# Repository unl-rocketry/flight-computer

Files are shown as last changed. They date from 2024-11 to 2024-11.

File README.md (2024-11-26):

# Flight Computer
A versatile, inexpensive, modular, and **open source** flight computer and altimeter
system for amateur and experimental rocketry.

All designs in this repository are licensed under the [**CERN-OHL-S v2 or any later 
version**](https://ohwr.org/project/cernohl/-/wikis/uploads/b236492596cfc91c12def7d50bbf7da0/cern_ohl_s_v2.pdf). 
Contributions are welcome!

# Core Board
This design should be capable of using input voltages from 3v → 16v on the
battery input to allow for a wide range of batteries to be used. It is designed
to control and independently fire up to 3 individual high power in-flight events
(eg. ejection charges).

## Built-in Sensors
The sensor package includes a Bosch BNO055 motion co-processor for acceleration,
magnetic heading, and 3d orientation. It also includes a Bosch BME280 sensor for
pressure (along with altitude), temperature, and humidity measurements. These
sensor measurements can be used for flight control, and can also be logged to a
MicroSD card mounted on the board for ease of data recovery.

## Toolchain Support
All programmable components of this board were selected to be compatible with
Rust-based microcontroller frameworks like Embassy, for ease of programming and
future extension of software capabilities.

## Images
front

back

# Expansion Modules
A major feature of the Core Board is the ability to be expanded by
connecting via an I2C (and hopefully in the future CAN Bus) connection to other
boards and sensors with the same connectors. These expansion  boards could
provide additional capabilities while being modular for quickly swapping and
replacing parts.

The connectors on the Core Board are compatible with any Adafruit Stemma QT or 
SparkFun Qwiic board, which immediately provides for a lot of options for
sensors without any design or soldering work needed.

In the future, this repository will host the KiCad files for expansion boards
created by UNL Aerospace Rocketry.

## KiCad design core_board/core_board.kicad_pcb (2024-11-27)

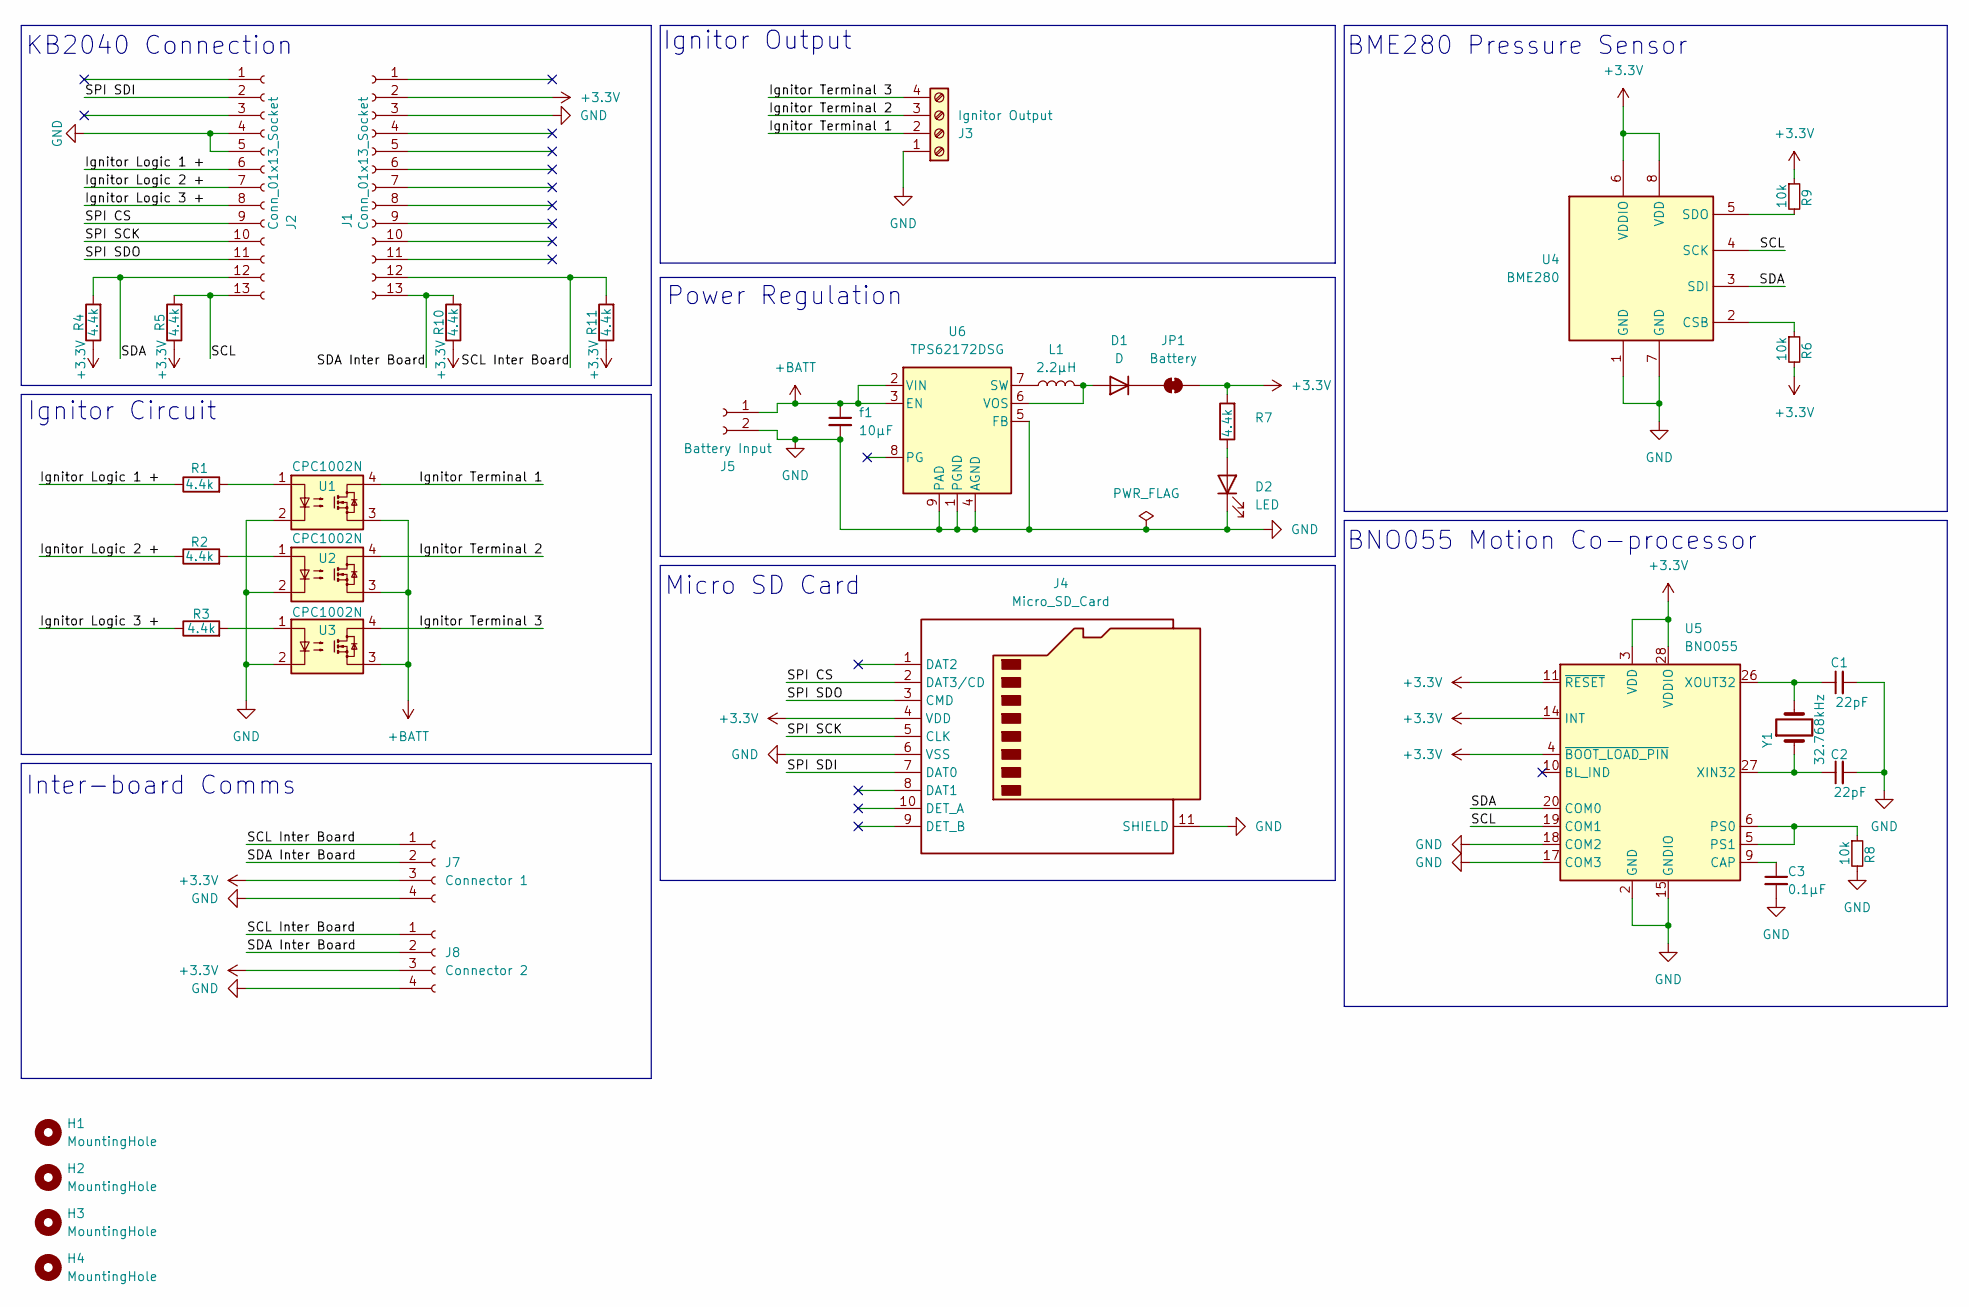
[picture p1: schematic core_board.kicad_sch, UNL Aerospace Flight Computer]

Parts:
C1, C2: 22pF; C_0603_1608Metric_Pad1.08x0.95mm_HandSolder
C3: 0.1µF; C_0603_1608Metric_Pad1.08x0.95mm_HandSolder
D1: D; D_0603_1608Metric_Pad1.05x0.95mm_HandSolder
D2: LED; LED_0603_1608Metric_Pad1.05x0.95mm_HandSolder
H1, H2, H3, H4: MountingHole; MountingHole_2.2mm_M2_ISO7380_Pad
J1, J2: Conn_01x13_Socket; PinHeader_1x13_P2.54mm_Vertical
J3: Ignitor Output; TerminalBlock_Phoenix_MPT-0,5-4-2.54_1x04_P2.54mm_Horizontal
J4: Micro_SD_Card; microSD_HC_Hirose_DM3D-SF
J5: Battery Input; JST_PH_S2B-PH-K_1x02_P2.00mm_Horizontal
J7: Connector 1; JST_SH_BM04B-SRSS-TB_1x04-1MP_P1.00mm_Vertical-CUSTOM
J8: Connector 2; JST_SH_BM04B-SRSS-TB_1x04-1MP_P1.00mm_Vertical-CUSTOM
JP1: Battery; SolderJumper-2_P1.3mm_Bridged_Pad1.0x1.5mm
L1: 2.2µH; L_0603_1608Metric_Pad1.05x0.95mm_HandSolder
R1, R2, R3, R4, R5, R7, R10, R11: 4.4k; R_0603_1608Metric_Pad0.98x0.95mm_HandSolder
R6, R8, R9: 10k; R_0603_1608Metric_Pad0.98x0.95mm_HandSolder
U1, U2, U3: CPC1002N; SOP-4_3.8x4.1mm_P2.54mm
U4: BME280; Bosch_LGA-8_2.5x2.5mm_P0.65mm_ClockwisePinNumbering
U5: BNO055; LGA-28_5.2x3.8mm_P0.5mm
U6: TPS62172DSG; WSON-8-1EP_2x2mm_P0.5mm_EP0.9x1.6mm_ThermalVias
Y1: 32.768kHz; Crystal_SMD_G8-2Pin_3.2x1.5mm_HandSoldering
f1: 10µF; C_0805_2012Metric_Pad1.18x1.45mm_HandSolder

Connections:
+3.3V: J1.2, J4.4 (VDD), J7.3, J8.3, JP1.2 (B), R4.1, R5.1, R6.2, R7.2, R9.1, R10.1, R11.1, U4.6 (VDDIO), U4.8 (VDD), U5.3 (VDD), U5.4 (~BOOT_LOAD_PIN), U5.11 (~RESET), U5.14 (INT), U5.28 (VDDIO)
+BATT: J5.1, U1.3, U2.3, U3.3, U6.2 (VIN), U6.3 (EN), f1.1
/Ignitor Logic 1 +: J2.6, R1.1
/Ignitor Logic 2 +: J2.7, R2.1
/Ignitor Logic 3 +: J2.8, R3.1
/Ignitor Terminal 1: J3.2, U1.4
/Ignitor Terminal 2: J3.3, U2.4
/Ignitor Terminal 3: J3.4, U3.4
/SCL: J2.13, R5.2, U4.4 (SCK), U5.19 (COM1)
/SCL Inter Board: J1.12, J7.1, J8.1, R11.2
/SDA: J2.12, R4.2, U4.3 (SDI), U5.20 (COM0)
/SDA Inter Board: J1.13, J7.2, J8.2, R10.2
/SPI CS: J2.9, J4.2 (DAT3/CD)
/SPI SCK: J2.10, J4.5 (CLK)
/SPI SDI: J2.2, J4.7 (DAT0)
/SPI SDO: J2.11, J4.3 (CMD)
GND: C1.2, C2.2, C3.2, D2.1 (K), J1.3, J2.4, J2.5, J3.1, J4.6 (VSS), J4.11 (SHIELD), J5.2, J7.4, J8.4, R8.2, U1.2, U2.2, U3.2, U4.1 (GND), U4.7 (GND), U5.2 (GND), U5.15 (GNDIO), U5.16 (GNDIO), U5.17 (COM3), U5.18 (COM2), U5.25 (GNDIO), U6.1 (PGND), U6.4 (AGND), U6.5 (FB), U6.9 (PAD), f1.2
unnamed: D1.2 (A), L1.2, U6.6 (VOS)
unnamed: D1.1 (K), JP1.1 (A)
unnamed: D2.2 (A), R7.1
unnamed: R1.2, U1.1
unnamed: R2.2, U2.1
unnamed: R3.2, U3.1
unnamed: R6.1, U4.2 (CSB)
unnamed: R9.2, U4.5 (SDO)
unnamed: C3.1, U5.9 (CAP)
unnamed: R8.1, U5.5 (PS1), U5.6 (PS0)
unnamed: C2.1, U5.27 (XIN32), Y1.1
unnamed: C1.1, U5.26 (XOUT32), Y1.2
unnamed: L1.1, U6.7 (SW)

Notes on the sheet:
Inter-board Comms
Micro SD Card
Ignitor Circuit
Power Regulation
KB2040 Connection
BME280 Pressure Sensor
Ignitor Output
BNO055 Motion Co-processor

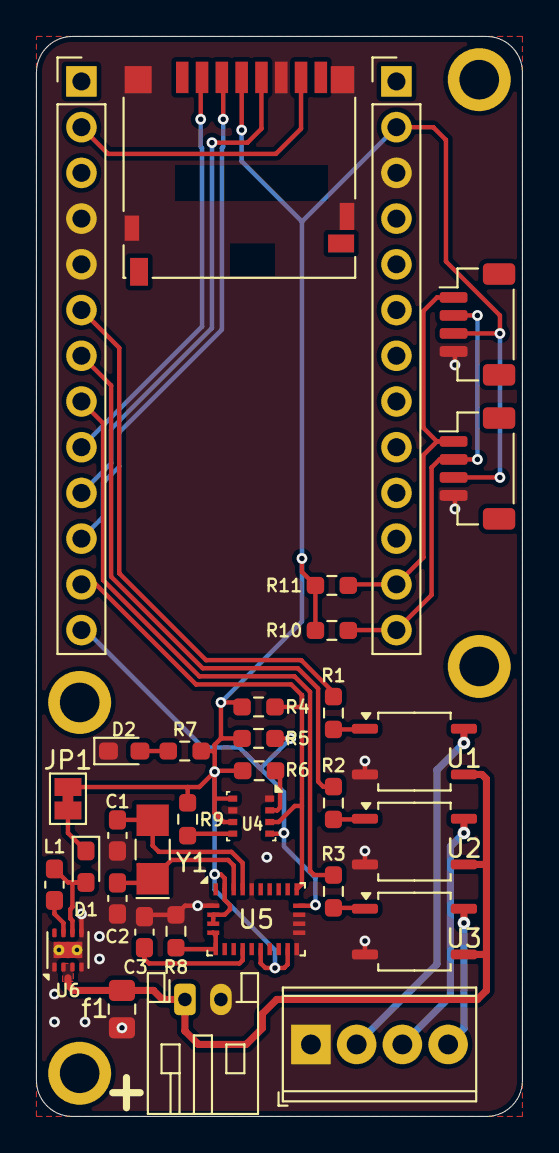
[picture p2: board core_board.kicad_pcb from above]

Board: 2 copper layers, 27.0 x 60.0 mm, 37 parts (0 on the bottom side), 30 nets.

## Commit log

2024-08-02 Layout finished for BNO055 and BME280
    [flight_computer.kicad_pcb, flight_computer.kicad_sch]
2024-08-02 Completed sensor layout
    [flight_computer.kicad_pcb, flight_computer.kicad_sch]
2024-08-02 Added voltage regulator
    [flight_computer.kicad_pcb, flight_computer.kicad_sch]
2024-08-02 Improved layout of connectors
    [flight_computer.kicad_pcb, flight_computer.kicad_sch]
2024-08-03 Added MicroSD card slot
    [flight_computer.kicad_pcb, flight_computer.kicad_sch]
2024-08-03 Added inter-board connectors to i2c
    [flight_computer.kicad_pcb, flight_computer.kicad_sch]
2024-08-04 Fixed back coppper layer island
    [flight_computer.kicad_pcb]
2024-08-20 Moved Core board to new folder
    [core_board.kicad_pcb, core_board.kicad_sch]
2024-08-31 Fixed connector compatibility with STEMMA QT and Qwiic
    [core_board.kicad_pcb, core_board.kicad_sch]
2024-08-31 Corrected DRC errors
    [core_board.kicad_pcb, core_board.kicad_sch]
2024-08-31 Set up files for easy fabrication output
    [core_board.kicad_pcb]
2024-09-03 Added Aerospace Club logo and gave mounting holes pads
    [core_board.kicad_pcb, core_board.kicad_sch]
2024-09-16 Added ground fill to top layer
    [core_board.kicad_pcb]
2024-11-25 Fixed small potential issues
    [core_board.kicad_pcb]
2024-11-26 Tweaked mounting holes, removed warning on back
    [core_board.kicad_pcb, core_board.kicad_sch]
2024-11-26 Added open hardware logo
    [core_board.kicad_pcb]
2024-11-26 Update README.md
    Updated readme with current information and images
2024-11-27 Improved PCB layout some more
    [core_board.kicad_pcb]
